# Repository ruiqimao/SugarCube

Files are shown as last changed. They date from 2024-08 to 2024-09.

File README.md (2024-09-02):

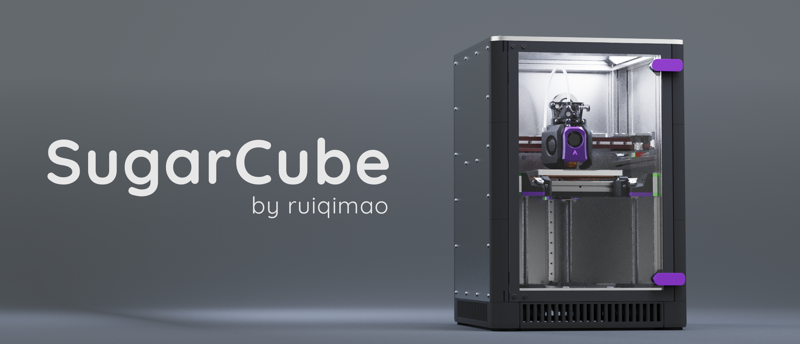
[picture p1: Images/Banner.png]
Banner


SugarCube is a compact, fully enclosed 3D printer, featuring:

* 120mm x 120mm x 120mm build space
* 153030 based frame
* CoreXY kinematics
* Kinematic triple Z
* Metal sandwich gantry
* NEMA17 XY motors
* Compatible with [Archetype toolhead ecosystem](https://github.com/Armchair-Heavy-Industries/Archetype)

## Dimensions

### Travel area
* Archetype Blackbird: 126mm x 122mm

### Outer dimensions

* Panel to panel: 272mm x 272mm x 395 mm
* With door handles and reverse bowden: 272mm x 288mm x 395mm

## BOM

Bill of materials can be found at [BOM.md](BOM.md).

## User Mods

Please submit any user mods at [SugarCube-UserMods](https://github.com/ruiqimao/SugarCube-UserMods).

## Acknowledgements

* @hartk for the renders
* @izziec for artistic inspiration
* @caza0455 and @burgo_enemy_of_thelettuce for pre-release review

## License

SugarCube is licensed under CC-BY-NC-SA-4.0. More details can be found at [LICENSE.md](LICENSE.md) and [https://creativecommons.org/licenses/by-nc-sa/4.0/](https://creativecommons.org/licenses/by-nc-sa/4.0/).

If you are interested in selling parts for SugarCube, please contact @ruiqimao on Discord.

<br>

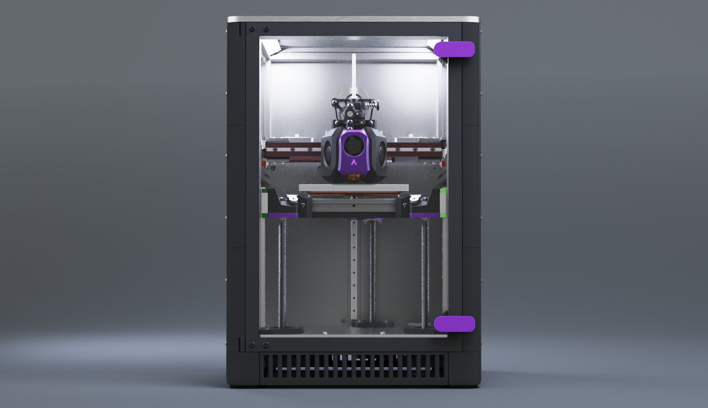
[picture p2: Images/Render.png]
Render


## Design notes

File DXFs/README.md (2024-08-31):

# Laser cut parts

These are the parts that should be laser cut/water jet/milled/etc.

| Part | Material | Thickness | Quantity |
|:-|:-:|:-:|:-:|
| Mid_Panel | Aluminum | 2mm | 2 |
| Deck_Panel | Aluminum | 3.2mm | 1 |
| Side_Panel | Aluminum | 3.2mm | 2 |
| Back_Top_Panel | Aluminum | 3.2mm | 1 |
| Back_Bottom_Panel | Aluminum | 3.2mm | 1 |
| Idler_Plate | Aluminum | 3.2mm | 4 |
| XY_Plate_A | Aluminum | 3.2mm | 2 |
| XY_Plate_B | Aluminum | 3.2mm | 2 |
| Motor_Top_Plate | Aluminum | 3.2mm | 1 |
| Motor_Bottom_Plate | Aluminum | 3.2mm | 1 |
| Tensioner_Plate | Aluminum | 3.2mm | 2 |
| SSR_Mount | Aluminum | 3.2mm | 1 |
| PSU_Mount | Aluminum | 3.2mm | 1 |
| Front_Door | Polycarbonate | 4.5mm | 1 |
| Top_Panel | Polycarbonate | 6mm | 1 |

## Tapped holes

### M3x0.5

All holes with 2.6mm diamter should be tapped M3x0.5:

* `XY_Plate_A`
  * 2 outer holes
* `PSU_Mount`
  * 4 PSU mounting holes

### M4x0.7

* `SSR_Mount`
  * 2 SSR mounting holes

## Countersunk holes

The highlighted holes should be countersunk 90°:

* `XY_Plate_A`
  * 3 rail carriage holes
* `Motor_Plate_Bottom`
  * 1 center hole
* `Mid_Panel`
  * All holes
* `Front_Door`
  * 4 left holes and 2 rightmost holes

## Reamed holes

All holes that hold a pin are undersized by 0.127mm (5 thou) and should be reamed to size.

### 3mm

All holes that that hold a 3mm pin:

* `Idler_Plate`
* `XY_Plate_A`
* `XY_Plate_B`
* `Motor_Top_Plate`
* `Motor_Bottom_Plate`

### 5mm

All holes that that hold a 5mm pin:

* `Idler_Plate`
* `XY_Plate_A`
* `XY_Plate_B`
* `Motor_Top_Plate`
* `Motor_Bottom_Plate`

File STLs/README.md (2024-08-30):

# FDM printed parts

## Recommended materials

All parts should be printed in ABS, ASA, or PC.

## Print settings

Use standard Voron print settings:

* 0.4mm line width
* 4 perimeters
* 5 top layers
* 5 bottom layers
* 40% infill

## Naming convention

Parts are named according to Voron naming convention:
* Files prefixed with `[a]_` should be printed in an accent color.
* Files suffixed with `_x*` should be printed in the specified quantity.
* Files with no `_x*` suffix should be printed once.

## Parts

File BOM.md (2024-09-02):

# Bill of Materials

## Printed parts

All required printed parts can be found in [STLs/](STLs). See the README in the folder for details.

## Laser cut parts

DXFs for all required laser cut parts can be found in [DXFs/](DXFs). See the README in the folder for details. Prepopulated SendCutSend carts are also available.

| Part | Quantity | Link |
|:-|:-:|:-|
| Gantry | 1 | [SendCutSend](https://cart.sendcutsend.com/yyqzdmpdw16p) |
| Panels | 1 | [SendCutSend](https://cart.sendcutsend.com/oz1hrsx3vmoi) |

## Frame

| Part | Quantity | Link |
|:-|:-:|:-|
| SugarCube Frame | 1 | [DLLPDF](https://dllpdf.com/sugarcube-frame) |

Drawings for the frame are available at [Drawings/Frame Extrusions.pdf](Drawings/Frame%20Extrusions.pdf).

## Bed heater

> [!WARNING]
> The bed heater drawing is untested.

A bed heater drawing is available at [Drawings/Bed Heater.pdf](Drawings/Bed%20Heater.pdf), which can be used to request a custom order at [Keenovo](https://www.keenovo.com/). Alternatively, a standard 100mm x 100mm or Voron 0 bed heater can be used as well.

Heater should be AC-powered and be at least 100W.

## Toolhead

SugarCube supports toolheads with belts facing outwards and spaced 10mm from the X extrusion (standard PFA). Belts are spaced 4mm apart (non-standard PFA).

The recommended toolhead for SugarCube is [Archetype Blackbird](https://github.com/Armchair-Heavy-Industries/Archetype). This document does not contain materials needed for the toolhead.

## Panels

| Part | Quantity | Link |
|:-|:-:|:-|
| 3mm cork sheet | As needed | [Amazon](https://www.amazon.com/gp/product/B0CFKTGZSB/) |
| Foil tape | As needed | [Amazon](https://www.amazon.com/dp/B0CNSXHK5C) |
| 15mm x 2mm foam tape | As needed | [Amazon](https://www.amazon.com/dp/B07L69KY7X) |

Side and back panels should be constructed using a sandwich of 3.2mm aluminum, 3mm cork, and foil tape. This provides both insulation and sound dampening.

The front panel requires ~1.5mm-2mm of foam for sealing.

## Motion

| Part | Quantity | Link |
|:-|:-:|:-|
| MGN7H-150 linear rail | 5 | [AliExpress (Youmetong)](https://www.aliexpress.us/item/3256801304880853.html) |
| MGN9H-200 linear rail | 1 | [AliExpress (Youmetong)](https://www.aliexpress.us/item/3256801245010834.html) |
| NEMA17 stepper motor (33mm shaft minimum | 2 |  | [StepperOnline](https://www.omc-stepperonline.com/nema-17-high-temp-stepper-motor-55ncm-77-93oz-in-55mm-round-shaft-insulation-class-h-180c-17hs19-2504s-h-v1)
| NEMA17 stepper motor w/ 150mm TR8x8 leadscrew | 3 | [Amazon](https://www.amazon.com/dp/B07YQLVZ86/) |
| POM TR8x8 leadscrew nut | 3 | [Amazon](https://www.amazon.com/gp/product/B07RJT1GD8/) |
| F623 bearing | 24 | [Misumi](https://us.misumi-ec.com/vona2/detail/221000528976/) |
| F695 bearing | 2 | [Misumi](https://us.misumi-ec.com/vona2/detail/221000528976/) |
| 3mm x 27mm pin | 12 | [Misumi](https://us.misumi-ec.com/vona2/detail/110100140710/) (cut to size) |
| 5mm x 27mm pin | 9 | [Misumi](https://us.misumi-ec.com/vona2/detail/110100140710/) (cut to size) |
| 1164mm closed loop GT2 belt | 2 | [Misumi](https://us.misumi-ec.com/vona2/detail/221004924958/?HissuCode=1164-2GT-6) |
| 20 tooth GT2 idler | 6 | [McMaster-Carr](https://www.mcmaster.com/3693N11/) |
| 20 tooth GT2 pulley | 2 | [McMaster-Carr](https://www.mcmaster.com/3684N12/) |
| 3mm x 5mm x 1mm shim | 34 | [RCAmerica](https://www.rcamerica.com/alu-shim-3x5x1-0mm-10-303141) |
| 5mm x 7mm x 0.5mm shim | 12 | [RCAmerica](https://www.rcamerica.com/shim-5x7x0-5-10-338586) |

## Fasteners

> [!WARNING]
> Fastener counts have not been verified. Please buy extras!

| Part | Quantity | Link |
|:-|:-:|:-|
| M2x5 FHCS | 6 | [McMaster-Carr](https://www.mcmaster.com/91294A003/) |
| M2x6 BHCS | 30 | [McMaster-Carr](https://www.mcmaster.com/90128A179/) |
| M2x8 BHCS | 12 | [McMaster-Carr](https://www.mcmaster.com/90128A178/) |
| M2.5x4 SHCS | 4 | [McMaster-Carr](https://www.mcmaster.com/91292A015/) |
| M3x6 BHCS | 56 | [Bolt Depot](https://boltdepot.com/Product-Details?product=15629) |
| M3x6 FHCS | 10 | [Bolt Depot](https://boltdepot.com/Product-Details?product=22621) |
| M3x6 ULP | 4 | [McMaster-Carr](https://www.mcmaster.com/90358A001/) |
| M3x8 BHCS | 8 | [Bolt Depot](https://boltdepot.com/Product-Details?product=15630) |
| M3x8 FHCS | 16 | [Bolt Depot](https://boltdepot.com/Product-Details?product=22622) |
| M3x8 SHCS | 44 | [Bolt Depot](https://boltdepot.com/Product-Details?product=23064) |
| M3x10 BHCS | 40 | [Bolt Depot](https://boltdepot.com/Product-Details?product=15631) |
| M3x10 SHCS | 10 | [Bolt Depot](https://boltdepot.com/Product-Details?product=23066) |
| M3x12 BHCS | 14 | [Bolt Depot](https://boltdepot.com/Product-Details?product=15632) |
| M3x12 FHCS | 2 | [Bolt Depot](https://boltdepot.com/Product-Details?product=22624) |
| M3x16 FHCS | 1 | [Bolt Depot](https://boltdepot.com/Product-Details?product=22625) |
| M3x16 SHCS | 6 | [Bolt Depot](https://boltdepot.com/Product-Details?product=23067) |
| M3x25 BHCS | 6 | [Bolt Depot](https://boltdepot.com/Product-Details?product=15635) |
| M3x25 SHCS | 2 | [Bolt Depot](https://boltdepot.com/Product-Details?product=23063) |
| M3x30 SHCS | 12 | [Bolt Depot](https://boltdepot.com/Product-Details?product=23061) |
| M3x35 BHCS | 2 | [Bolt Depot](https://boltdepot.com/Product-Details?product=15293) |
| M3x35 SHCS | 8 | [Bolt Depot](https://boltdepot.com/Product-Details?product=23069) |
| M3x40 BHCS | 6 | [Bolt Depot](https://boltdepot.com/Product-Details?product=15294) |
| M4x6 BHCS | 2 | [Bolt Depot](https://boltdepot.com/Product-Details?product=15636) |
| M5x30 BHCS | 4 | [Bolt Depot](https://boltdepot.com/Product-Details?product=15651) |
| M3 heatset insert | 36 | [McMaster-Carr](https://www.mcmaster.com/94180A331/) |
| M3 square nut | 4 | [McMaster-Carr](https://www.mcmaster.com/97259A101/) |
| M3 hex nut | 150 | [McMaster-Carr](https://www.mcmaster.com/90870A113/) |
| M3 nylock | 6 | [McMaster-Carr](https://www.mcmaster.com/90576A102/) |
| M4 knurled nut | 3 | [McMaster-Carr](https://www.mcmaster.com/90368A200/) |
| M5 heatset insert | 4 | [McMaster-Carr](https://www.mcmaster.com/94180A361/) |
| LDO M2 nut bar | 5 | [KB3D](https://kb-3d.com/store/frame-enclosure/401-ldo-t-nut-bar-kit-for-voron-v0-1639078625144.html) |

## Electronics

| Part | Quantity | Link |
|:-|:-:|:-|
| Meanwell UHP-200-24 PSU | 1 | [DigiKey](https://www.digikey.com/en/products/detail/mean-well-usa-inc/UHP-200-24/7707239) |
| Crydom D2440 SSR | 1 | [DigiKey](https://www.digikey.com/en/products/detail/sensata-crydom/D2440/221764) |
| IEC320-C14 Inlet | 1 | [DigiKey](https://www.digikey.com/en/products/detail/adam-tech/IEC-GS-1-100/9831135) |
| Raspberry Pi 5 8GB | 1 | [DigiKey](https://www.digikey.com/en/products/detail/raspberry-pi/SC1112/21658257) |
| 5015 axial fan | 2 | [DigiKey](https://www.digikey.com/en/products/detail/delta-electronics/AFB0524HHB/2560406) |
| 5015 blower fan | 1 | [DigiKey](https://www.digikey.com/en/products/detail/delta-electronics/BFB0524HH/1014447) |
| Fysetc S6 | 1 | [AliExpress](https://www.aliexpress.us/item/2255800159054476.html) |
| TMC5160 stepstick | 6 | [Watterott](https://shop.watterott.com/SilentStepStick-TMC5160-Stepper-motor-driver-HV-V15) |
| Beacon Rev H | 1 | [Beacon](https://beacon3d.com/product/beacon-h/) |

## Miscellaneous

| Part | Quantity | Link |
|:-|:-:|:-|
| 10mm x 3mm countersunk N52 magnet pair | 8 pairs | [K&J Magnetics](https://www.kjmagnetics.com/proddetail.asp?prod=R622CS-P-N52) |
| Rubber grommet | 2 | [McMaster-Carr](https://www.mcmaster.com/9307K65/) |
| 38mm x 19mm rubber feet | 4 | [KB3D](https://kb-3d.com/store/hardware/458-rubber-machine-foot-amplifier-38mm-x-19mm-set-of-4-1642262899696.html) |
| 15.5mm x 3mm ID x 4mm OD PTFE tube | 2 | [Amazon](https://www.amazon.com/dp/B07B8CK8L9/) |
| 120mm x 120mm aluminum bed | 1 | [DFH](https://dfh.fm/products/ultra-flat-black-aluminum-beds-for-ants-by-lightweight-labware) |
| 120mm x 120mm magnet sheet | 1 | [McMaster-Carr](https://www.mcmaster.com/7301T25/) (cut to size) |
| 120mm x 120mm spring steel sheet | 1 | [Fabreeko](https://www.fabreeko.com/products/open-beta-semi-satin-thin-dual-sided-textured-beds-by-honeybadger) |

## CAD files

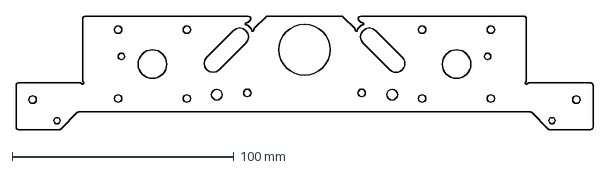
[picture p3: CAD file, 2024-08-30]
DXFs/Motor_Top_Plate.dxf
260.0 x 51.0 mm

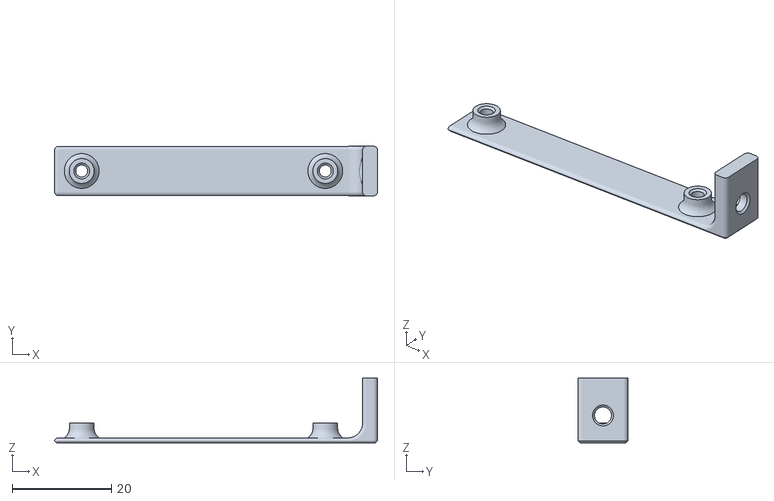
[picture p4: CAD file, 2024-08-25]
STLs/Electronics/Pi_Mount_x2.stl
65.0 x 10.0 x 13.0

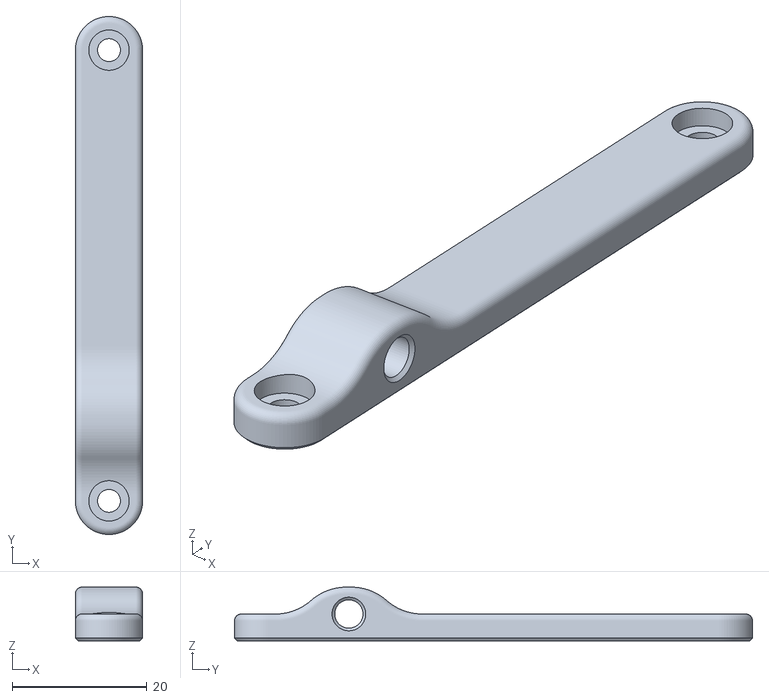
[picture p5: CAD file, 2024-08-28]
STLs/Panels/Reverse_Bowden_Holder.stl
10.0 x 77.0 x 8.00

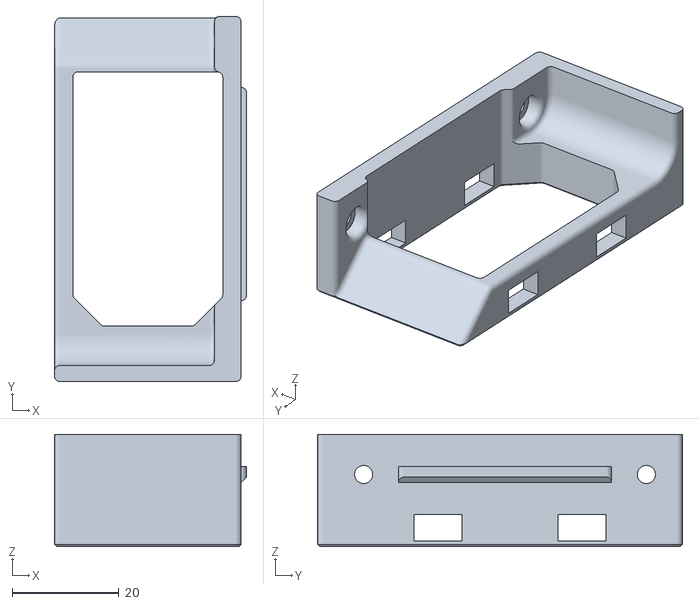
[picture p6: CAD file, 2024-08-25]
STLs/Skirt/Inlet_Mount.stl
36.0 x 68.4 x 21.0

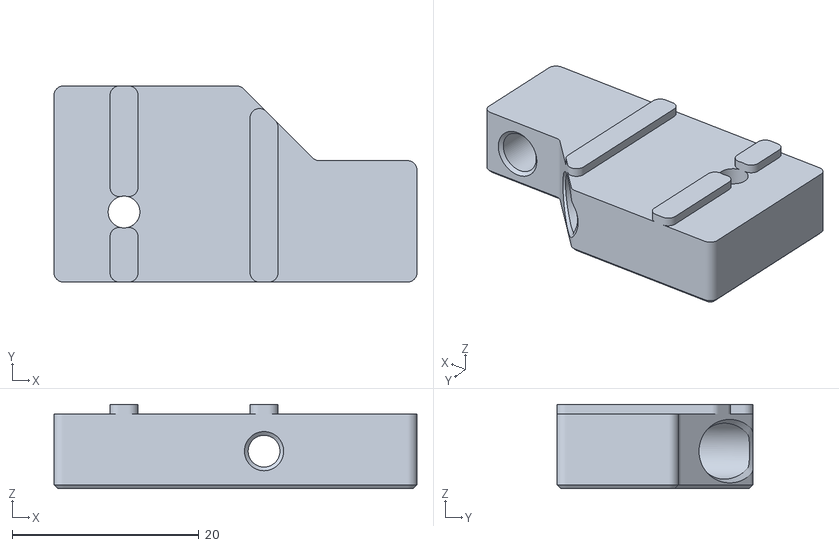
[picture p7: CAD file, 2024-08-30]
STLs/XY/Motor_Drive_Spacer_Lower_Left.stl
38.9 x 21.0 x 9.00

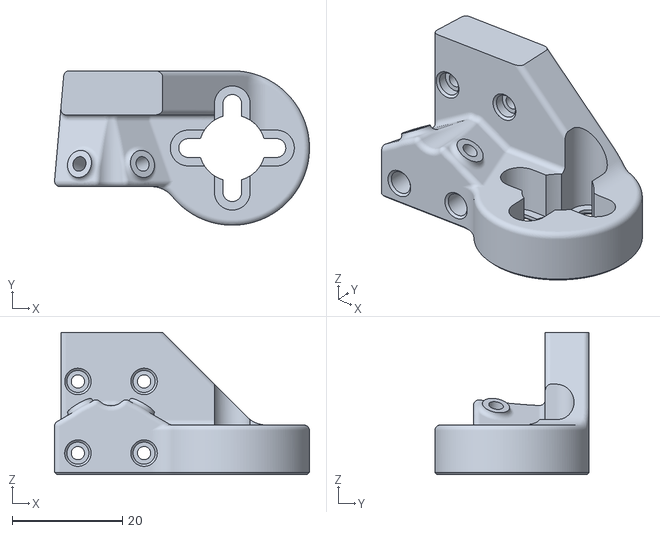
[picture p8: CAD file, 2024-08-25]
STLs/Z/Z_Carriage_Rear.stl
46.2 x 28.0 x 25.8

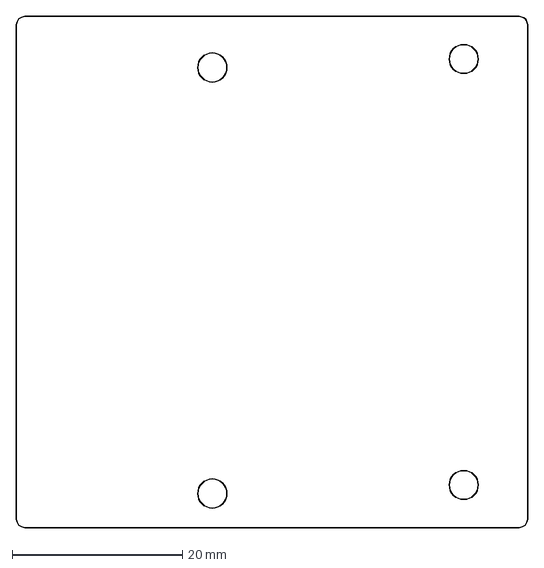
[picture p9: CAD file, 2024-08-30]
DXFs/SSR_Mount.dxf
60.0 x 60.0 mm

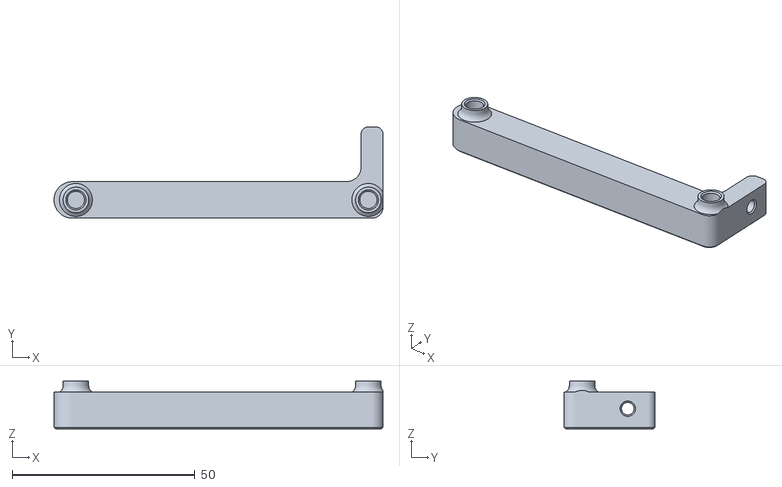
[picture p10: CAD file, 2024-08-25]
STLs/Electronics/Fysetc_S6_Mount.stl
90.0 x 25.0 x 13.0

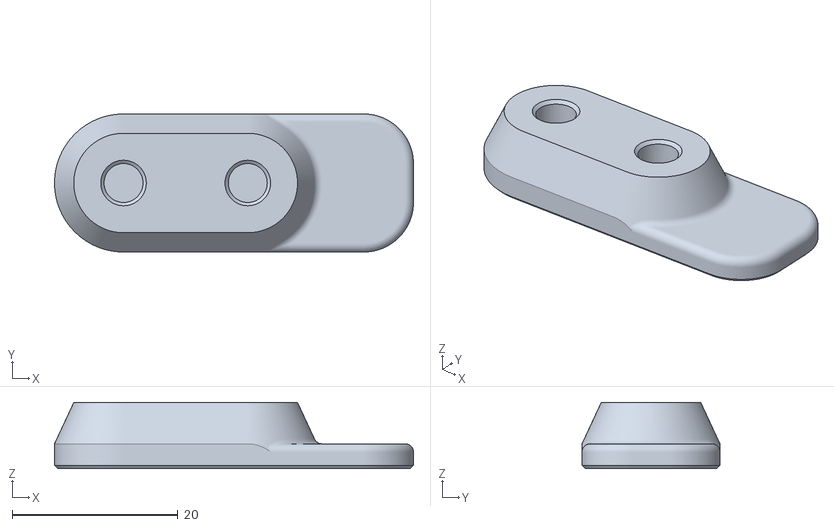
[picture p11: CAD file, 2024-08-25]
STLs/Panels/[a]_Door_Handle_x2.stl
43.3 x 16.7 x 8.00

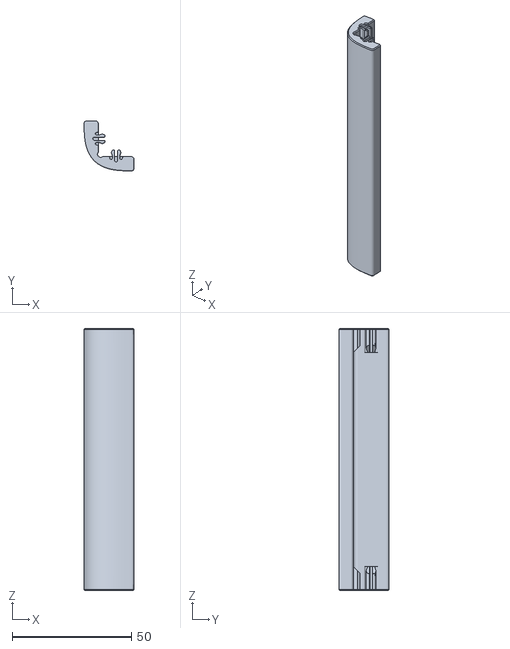
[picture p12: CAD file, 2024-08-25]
STLs/Skirt/Corner_Cover_A_x6.stl
21.0 x 21.0 x 110.0

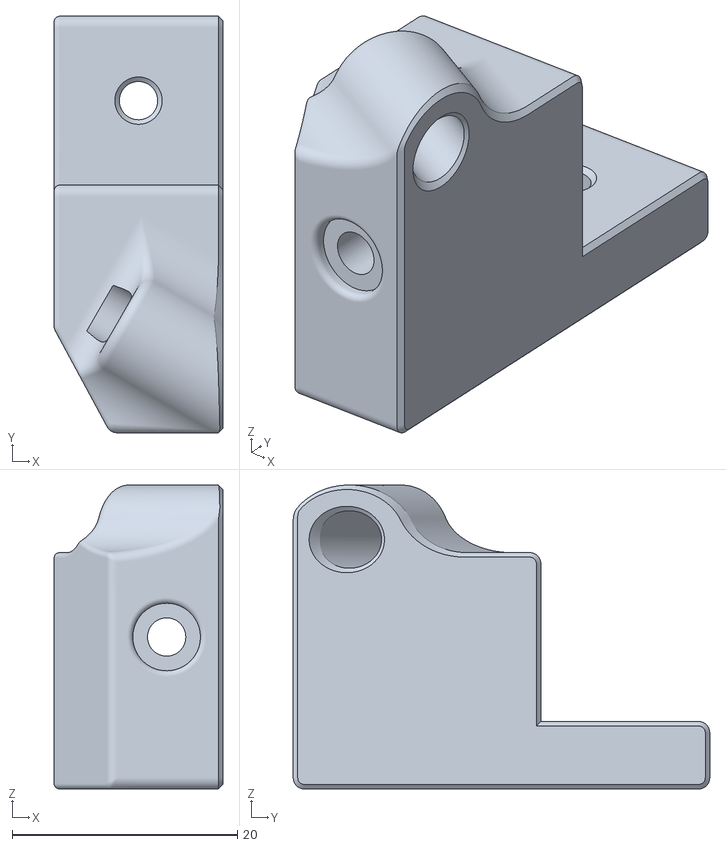
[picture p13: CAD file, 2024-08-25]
STLs/Z/Bed_Carrier_Right.stl
15.0 x 37.0 x 27.0

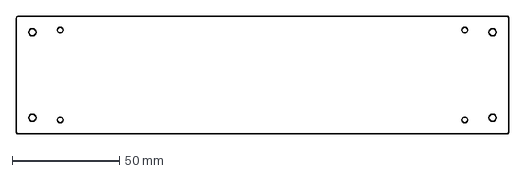
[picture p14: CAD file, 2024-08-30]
DXFs/PSU_Mount.dxf
230.0 x 55.0 mm

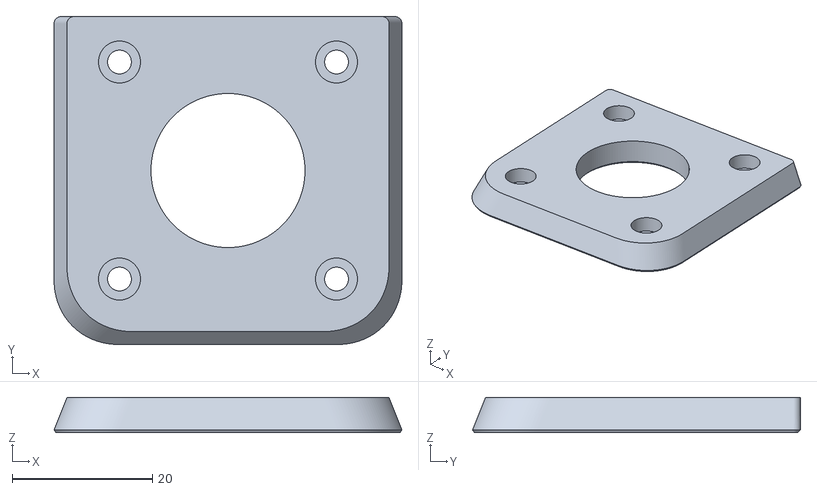
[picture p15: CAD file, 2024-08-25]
STLs/Panels/Z_Motor_Cover_Rear.stl
49.7 x 46.9 x 5.00

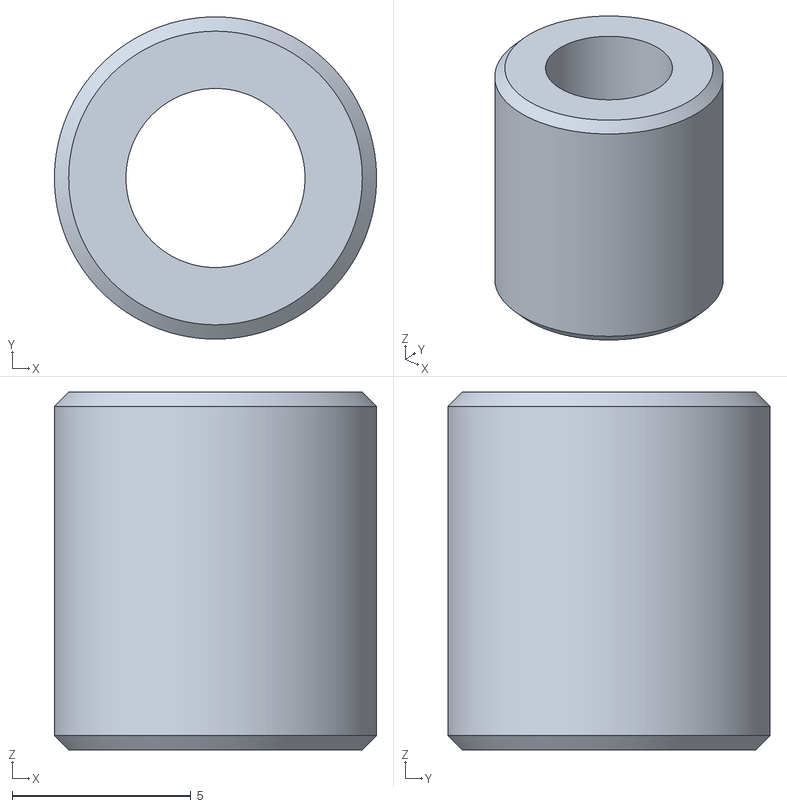
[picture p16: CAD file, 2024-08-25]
STLs/XY/Toothed_Idler_Spacer_x6.stl
9.00 x 9.00 x 10.0

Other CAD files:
STLs/XY/Motor_Drive_Spacer_Lower_Right.stl
STLs/Skirt/Corner_Cover_Hinge_Upper.stl
STLs/Z/[a]_Z_Carriage_Accent_Right.stl
DXFs/Back_Bottom_Panel.dxf
DXFs/Back_Top_Panel.dxf
DXFs/Deck_Panel.dxf
DXFs/Front_Door.dxf
DXFs/Idler_Plate_x4.dxf
DXFs/Mid_Panel_x2.dxf
DXFs/Motor_Bottom_Plate.dxf
DXFs/Side_Panel_x2.dxf
DXFs/Tensioner_Plate_x2.dxf
DXFs/Top_Panel.dxf
DXFs/XY_Plate_A_x2.dxf
DXFs/XY_Plate_B_x2.dxf
STLs/Panels/Door_Latch_Lower.stl
STLs/Panels/Door_Latch_Upper.stl
STLs/Panels/Mid_Panel_Mount_x4.stl
STLs/Panels/Mid_Panel_Spacer_x2.stl
STLs/Panels/Z_Motor_Cover_x2.stl
STLs/Skirt/Corner_Cover_B_x4.stl
STLs/Skirt/Corner_Cover_Hinge_Lower.stl
STLs/Skirt/Foot_x4.stl
STLs/Skirt/Hinge_x2.stl
STLs/Skirt/Skirt_Rear.stl
STLs/XY/Front_Idler_Spacer_Lower_Left.stl
STLs/XY/Front_Idler_Spacer_Lower_Right.stl
STLs/XY/Front_Idler_Spacer_x2.stl
STLs/XY/Motor_Drive_Bearing_Holder_x2.stl
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

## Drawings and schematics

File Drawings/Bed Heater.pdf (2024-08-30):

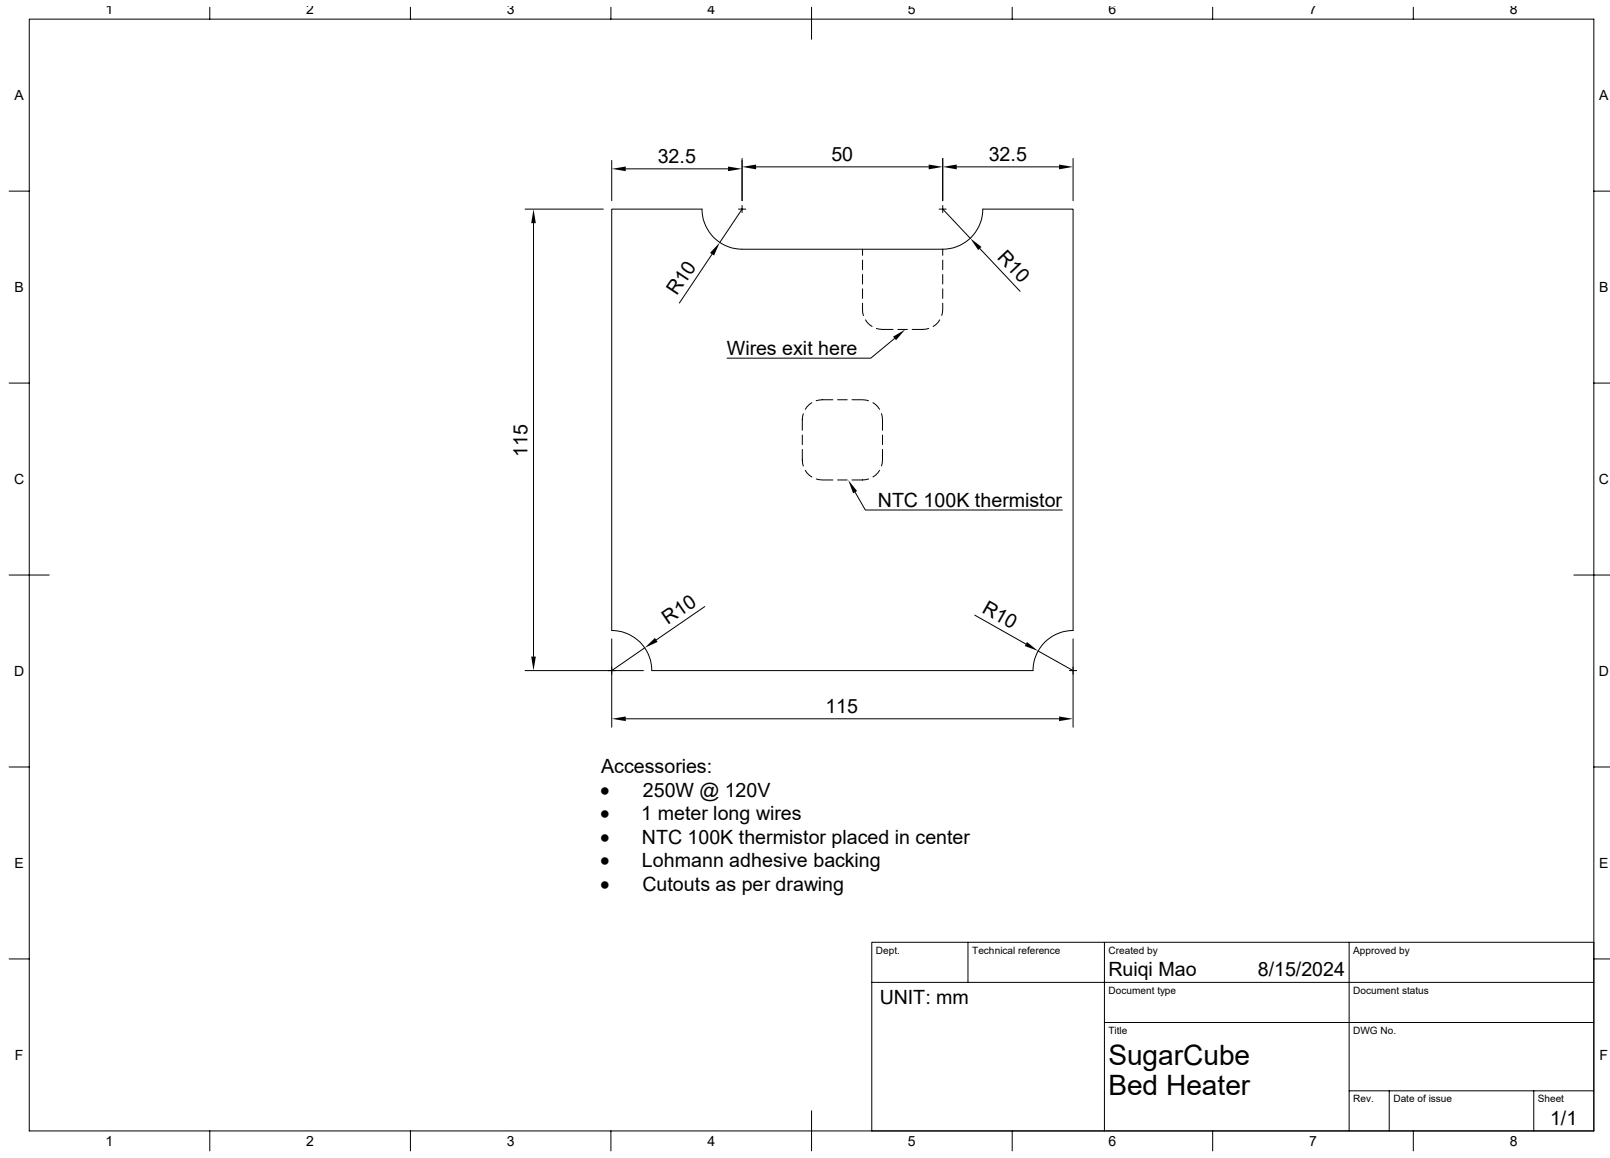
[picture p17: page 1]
8 BCDEF; ABCDEF Dept.; Technical reference; Created by; Approved by Document type; Document status Title; DWG No. Rev.; Date of issue; Sheet 8/15/2024; 1/1 Bed Heater SugarCube Ruiqi Mao 32.5; 32.5 R¹⁰

115 UNIT: mm NTC 100K thermistor Wires exit here Accessories: · 250W @ 120V · 1 meter long wires · NTC 100K thermistor placed in center · Lohmann adhesive backing · Cutouts as per drawing115

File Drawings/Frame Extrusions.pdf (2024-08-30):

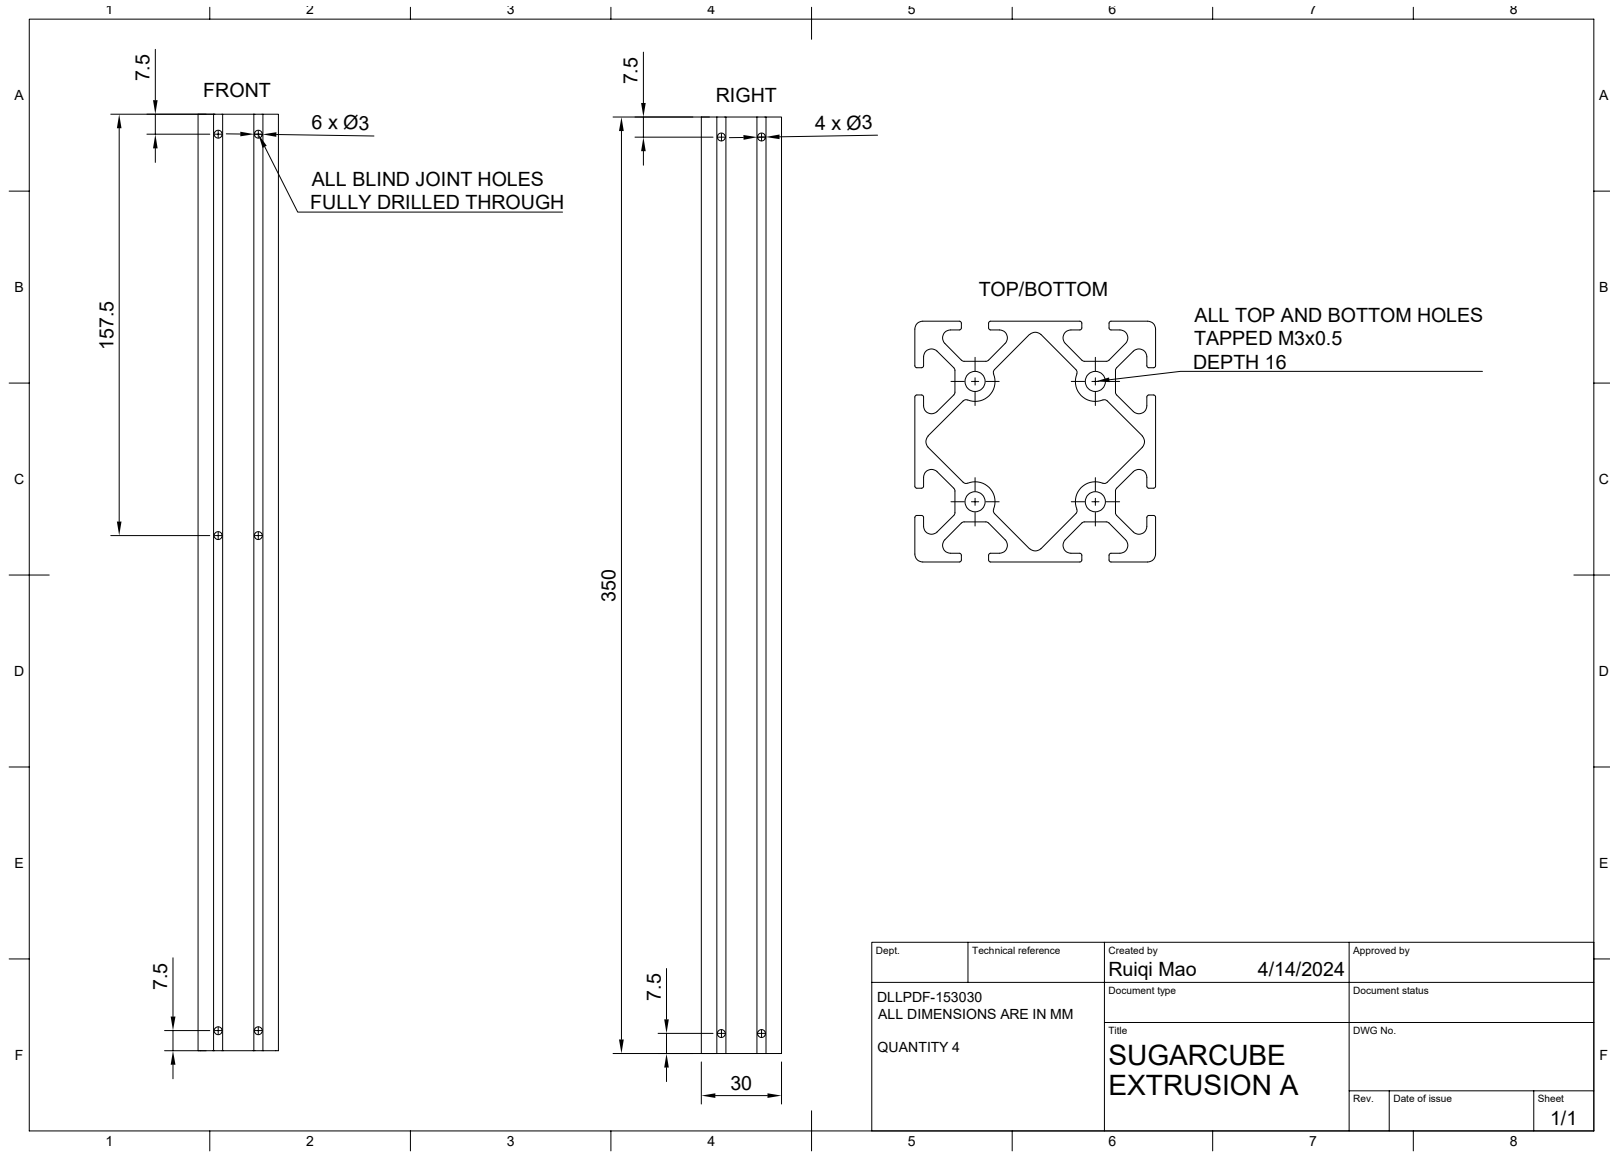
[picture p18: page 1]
8 BCDEF; ABCDEF Dept.; Technical reference; Created by; Approved by Document type; Document status Title; DWG No. Rev.; Date of issue; Sheet 4/14/2024; 1/1 EXTRUSION A SUGARCUBE Ruiqi Mao FRONT; 7.5 RIGHT

350 ALL BLIND JOINT HOLES FULLY DRILLED THROUGH 30 6 x Ø3 4 x Ø3DLLPDF-153030 ALL DIMENSIONS ARE IN MM QUANTITY 4

7.5 TOP/BOTTOM ALL TOP AND BOTTOM HOLES TAPPED M3x0.5 DEPTH 16

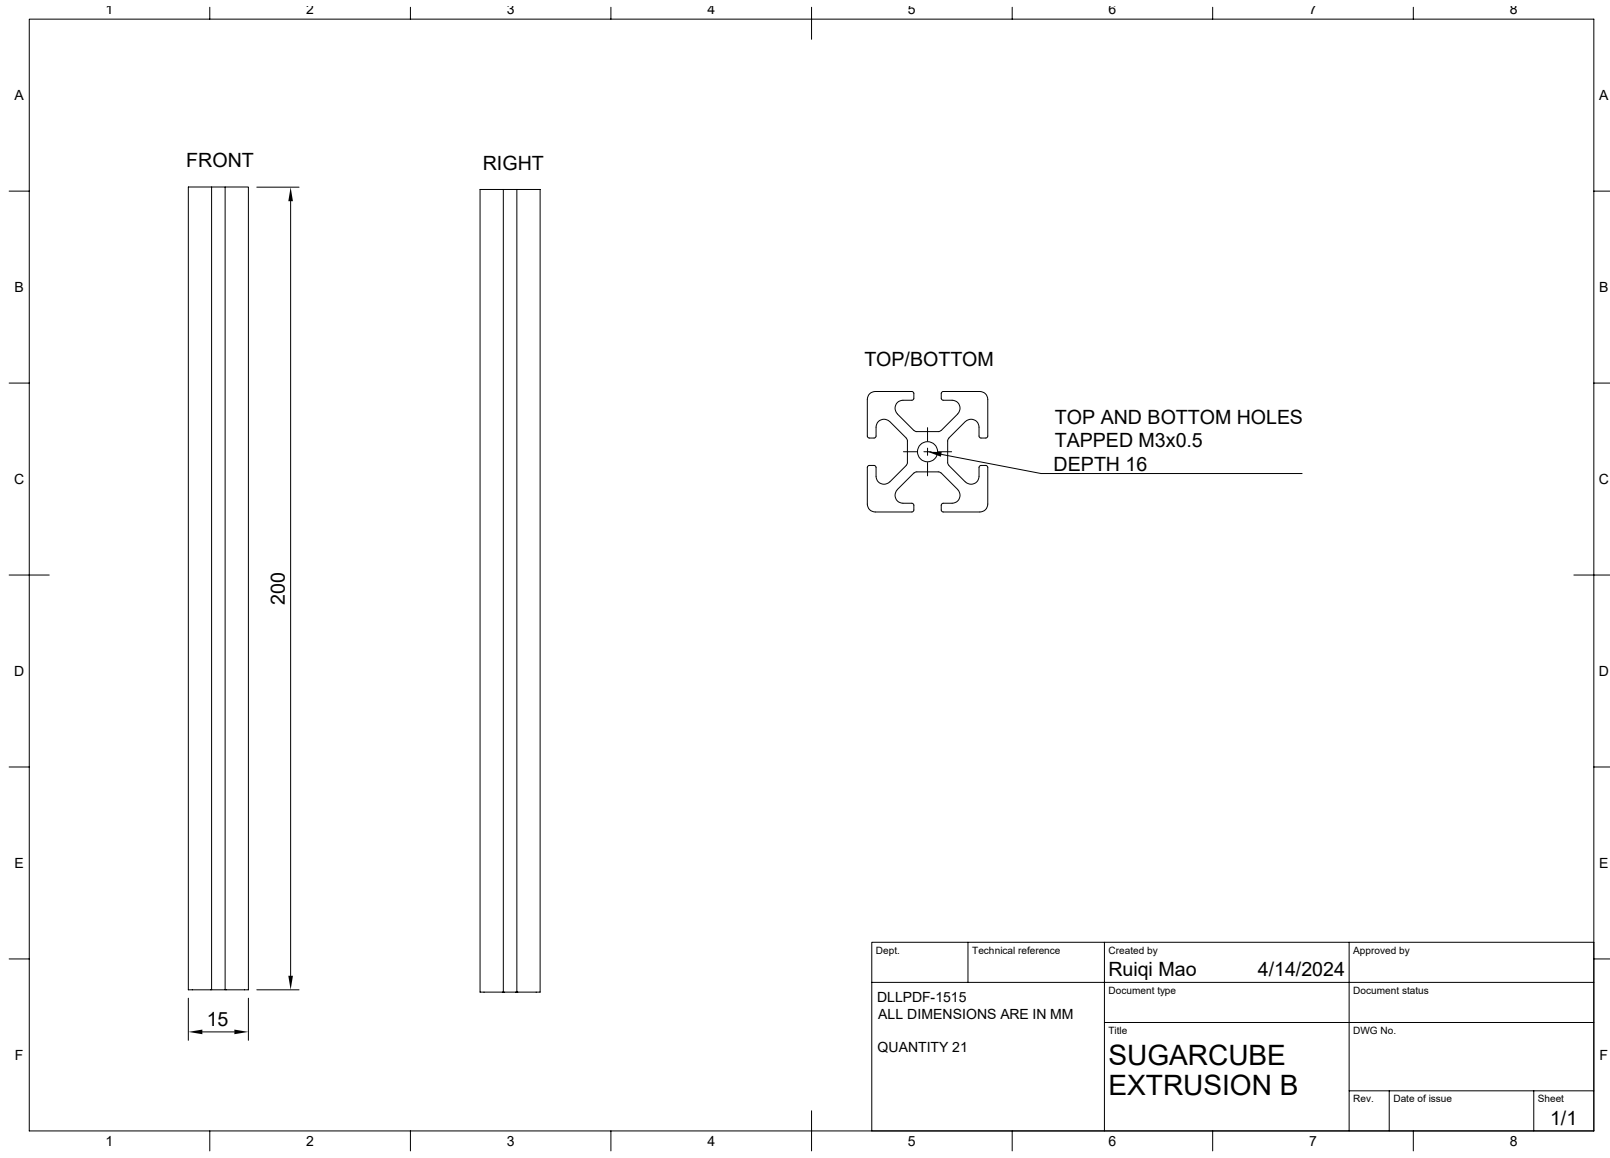
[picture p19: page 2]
8 BCDEF; ABCDEF Dept.; Technical reference; Created by; Approved by Document type; Document status Title; DWG No. Rev.; Date of issue; Sheet 4/14/2024; 1/1 EXTRUSION B SUGARCUBE Ruiqi Mao FRONT

200 RIGHT TOP/BOTTOM TOP AND BOTTOM HOLES TAPPED M3x0.5 DEPTH 16 15 DLLPDF-1515 ALL DIMENSIONS ARE IN MM QUANTITY 21

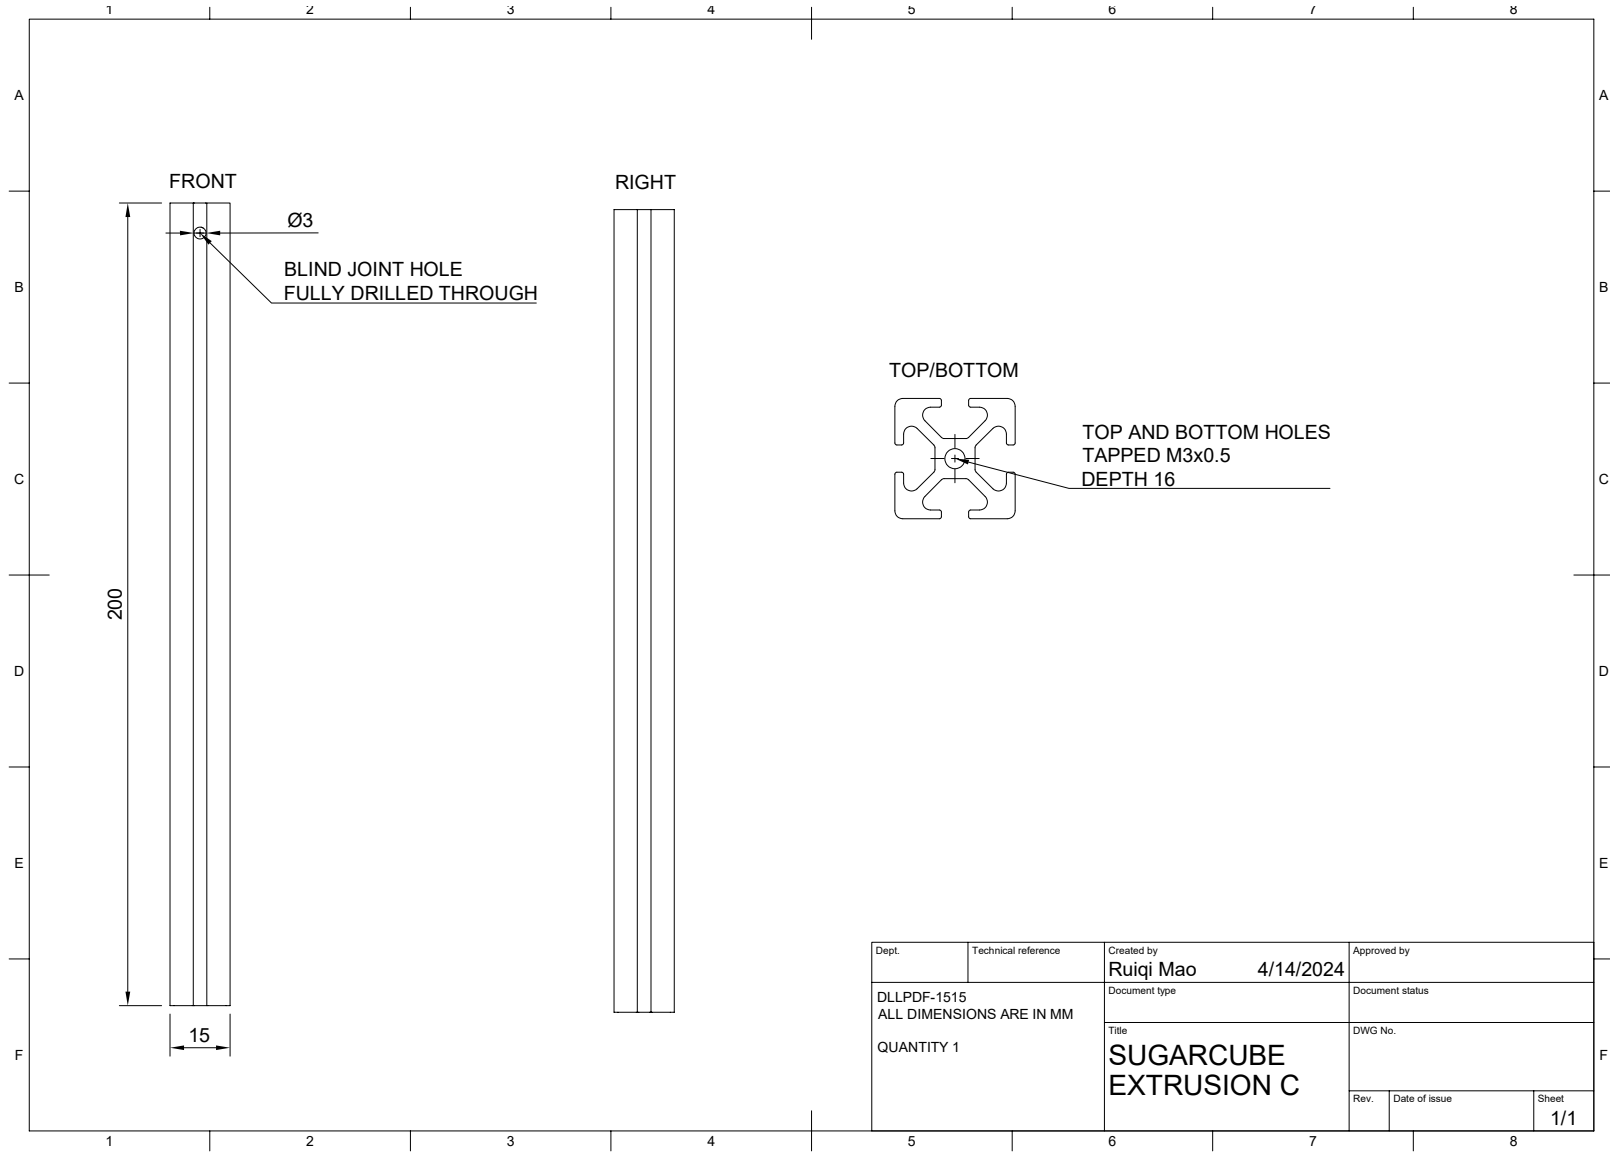
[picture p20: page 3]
8 BCDEF; ABCDEF Dept.; Technical reference; Created by; Approved by Document type; Document status Title; DWG No. Rev.; Date of issue; Sheet 4/14/2024; 1/1 EXTRUSION C SUGARCUBE Ruiqi Mao FRONT

200 15 Ø3 BLIND JOINT HOLE FULLY DRILLED THROUGH RIGHT TOP AND BOTTOM HOLES TAPPED M3x0.5 DEPTH 16 TOP/BOTTOM DLLPDF-1515 ALL DIMENSIONS ARE IN MM QUANTITY 1

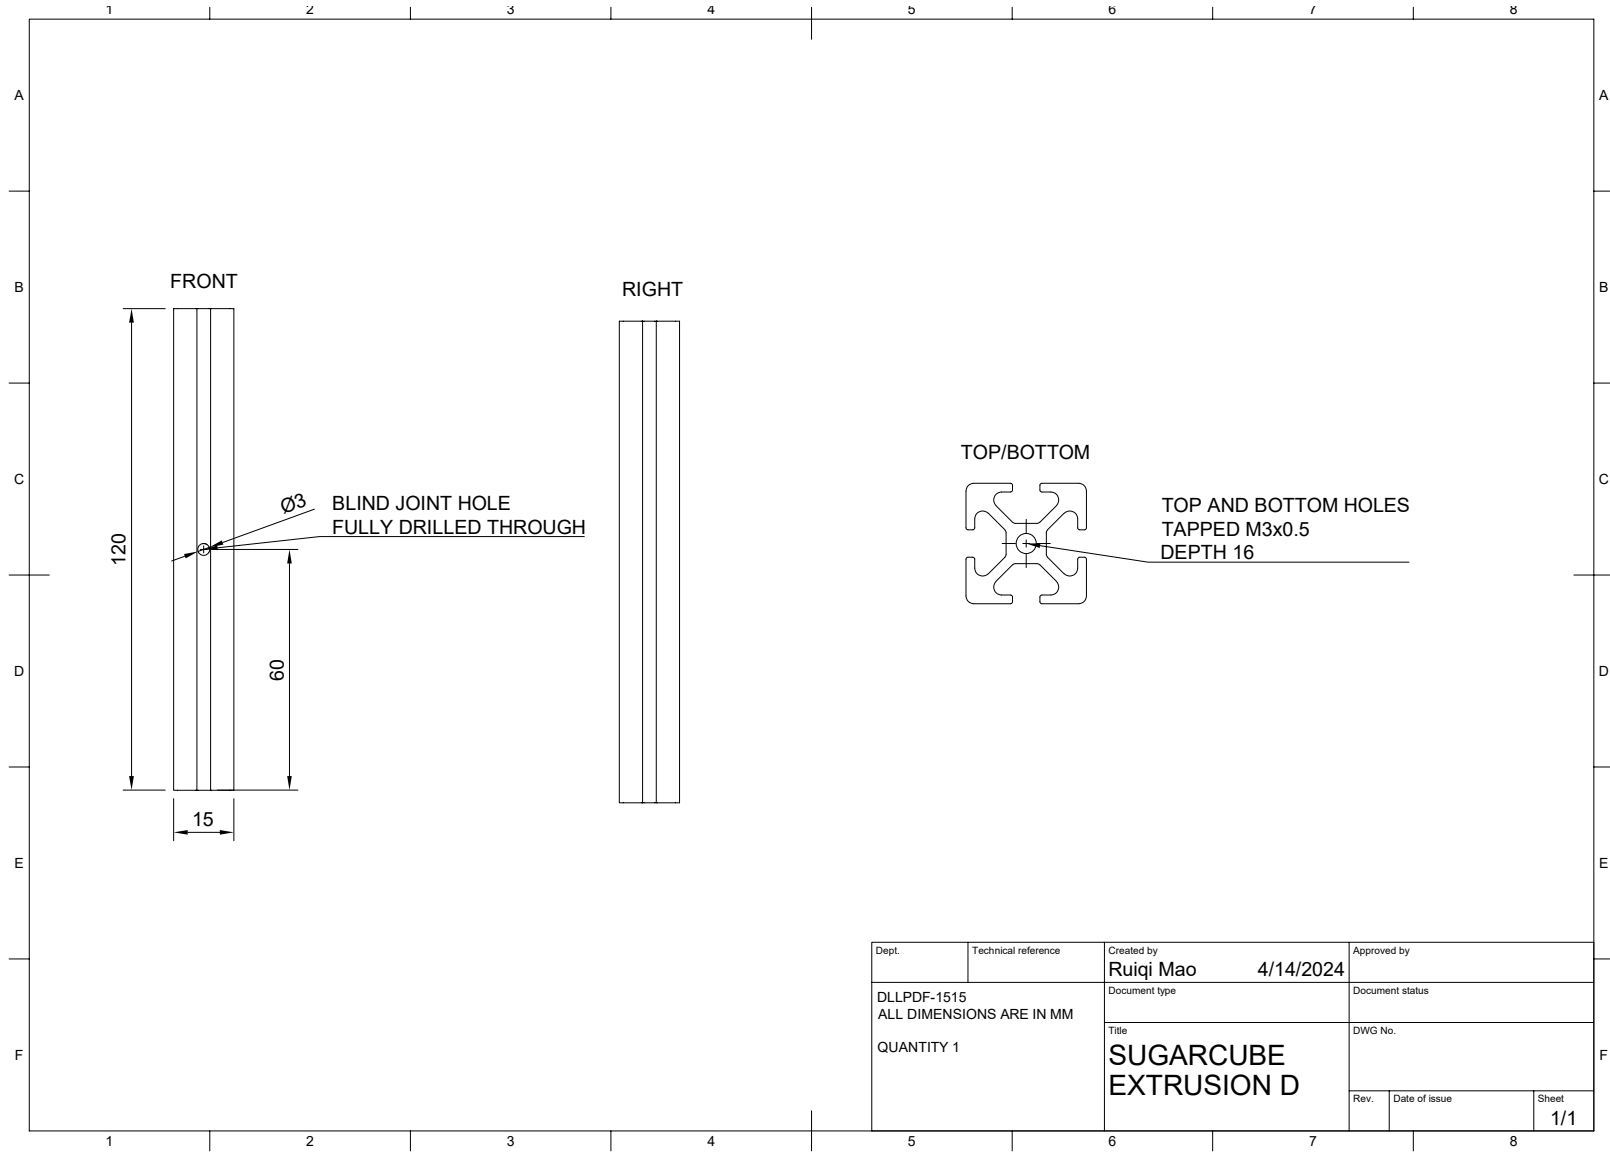
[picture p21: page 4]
8 BCDEF; ABCDEF Dept.; Technical reference; Created by; Approved by Document type; Document status Title; DWG No. Rev.; Date of issue; Sheet 4/14/2024; 1/1 EXTRUSION D SUGARCUBE Ruiqi Mao 15

120 FRONT Ø3 BLIND JOINT HOLE FULLY DRILLED THROUGH RIGHT TOP/BOTTOM TOP AND BOTTOM HOLES TAPPED M3x0.5 DEPTH 16 DLLPDF-1515 ALL DIMENSIONS ARE IN MM QUANTITY 1

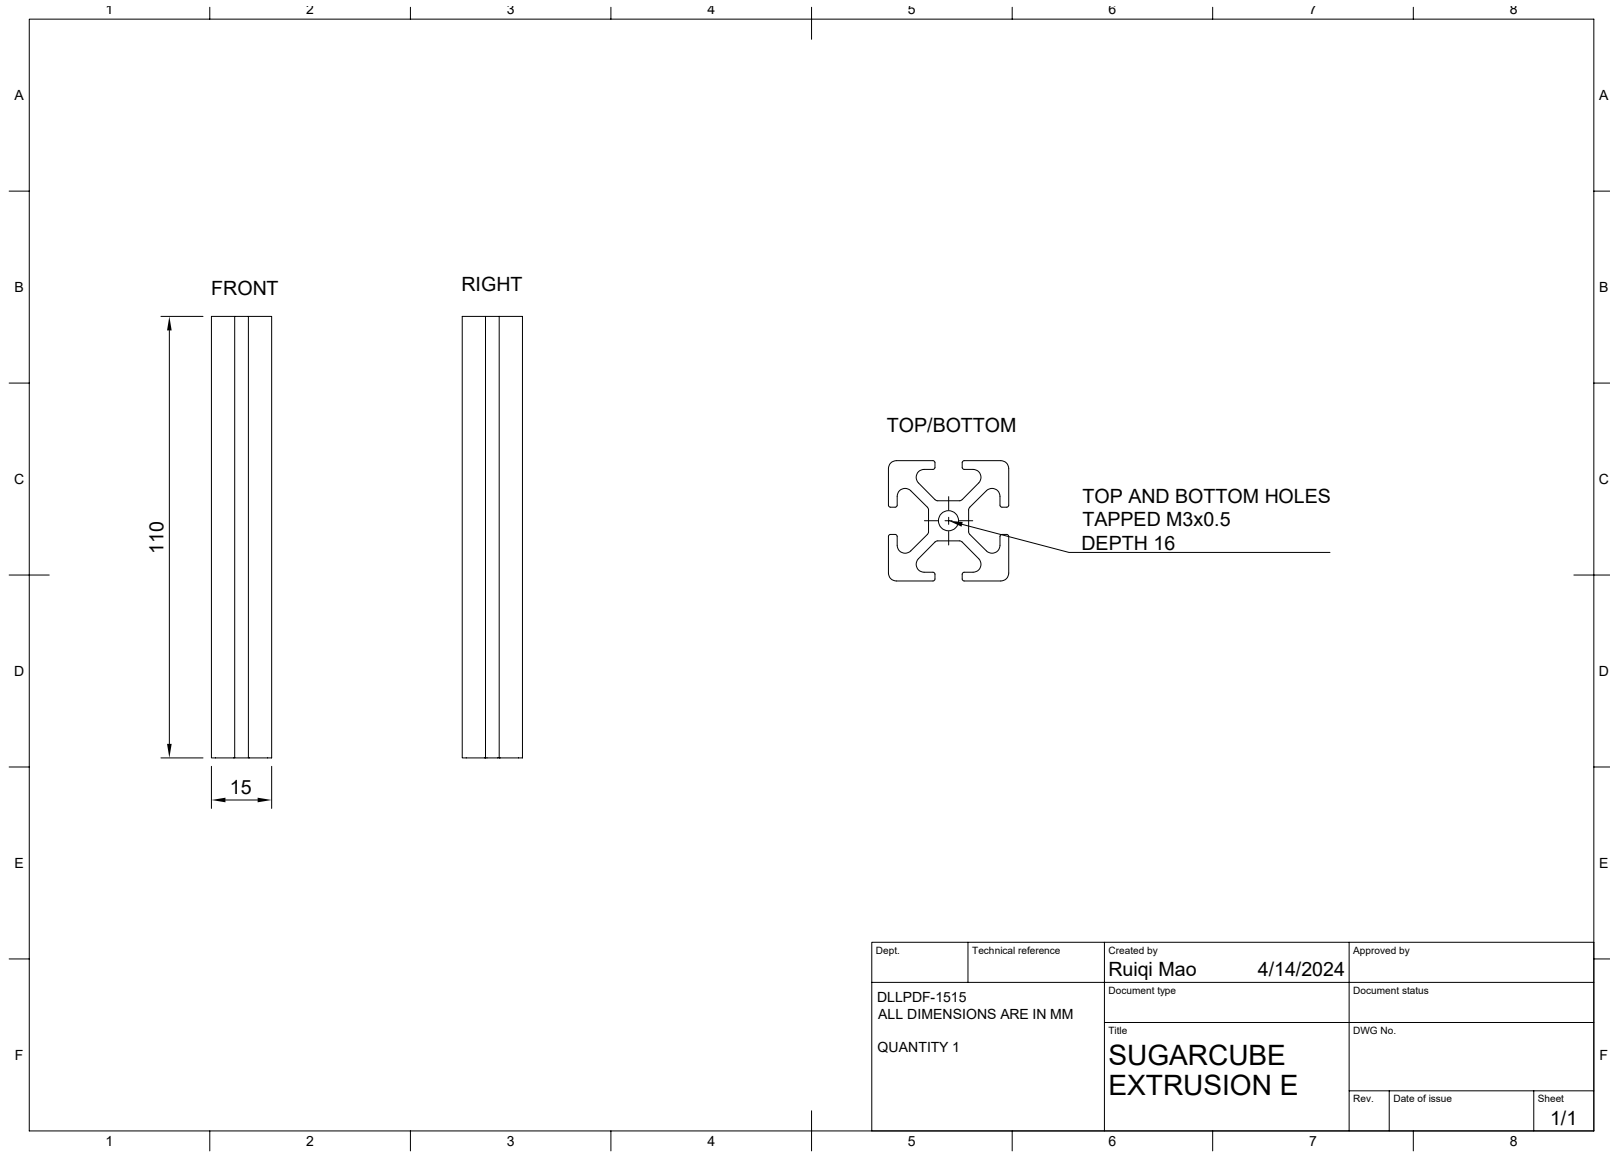
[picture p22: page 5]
8 BCDEF; ABCDEF Dept.; Technical reference; Created by; Approved by Document type; Document status Title; DWG No. Rev.; Date of issue; Sheet 4/14/2024; 1/1 EXTRUSION E SUGARCUBE Ruiqi Mao FRONT

110 15 RIGHT TOP/BOTTOM TOP AND BOTTOM HOLES TAPPED M3x0.5 DEPTH 16 DLLPDF-1515 ALL DIMENSIONS ARE IN MM QUANTITY 1

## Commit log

2024-08-25 Add render and missing Toothed_Idler_Spacer
    [Toothed_Idler_Spacer_x6.stl]
2024-08-25 Add CAD
2024-08-28 Fix incorrect chamfer on reverse bowden holder
    [Back_Bottom_Panel.dxf, Reverse_Bowden_Holder.stl]
2024-08-28 Fix reversed leadscrews
2024-08-30 Minor updates
    - Add extra mounting to motor drive
    - Replace plastic SSR and PSU mounts with metal
    [D2440_Mount.stl, Motor_Drive_Spacer_Lower_Left.stl, Motor_Drive_Spacer_Lower_Right.stl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]
